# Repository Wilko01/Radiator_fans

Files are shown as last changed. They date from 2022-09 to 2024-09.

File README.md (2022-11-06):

# Radiator fan controlled
The radiator fan is used to control the airflow of the radiators to be able to heat the house via low temperatures.

Pictures of the parts

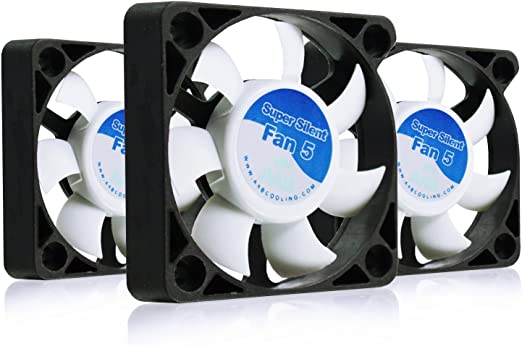
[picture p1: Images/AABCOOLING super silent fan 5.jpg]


## Description and operation instructions
The fans are turned on when a certain temperature of the radiator is detected and turned off when it is below another temperature value. The fans are controlled via different levels where at lower temperature levels the fan runs at a lower speed and when the temperature level is high the fan runs at a higher speed. The logic is running on the ESP32. To be able to override the logic there is an override variable which enables remote control and bypasing the ESP32 fan control. 
The fans are modular build where the first unit is the master which has 3 fans and the micro controller ESP32. It can be extended with a number of modules which act as slaves. Each module contains 3 fans. Tested with a maximum of 4 modules. 1 master and 3 slaves.

 ## Technical description
The ESP32 provides an analogue value which is fed into a transistor. The transistor amplifies the voltage and is typically operating between 5V and 12V. Lower than 5V will stop fans as they are not PWM fans. The ESP32 is running ESPHOME and connected to Home Assistant. The sensor for the temperature is included in the master module. Slaves will get the analogue value from the master and amplified it via the transistor. A trim potential meter is used to tune the master and slave modules as there are voltage losses when connecting multiple modules. By tuning the speed of all fans of all modules can be aligned. Best is to set the 500 Ohm potential meter to 250 Ohm before soldering it in. This provides space to tweak. See the next paragraph for the calibration of the fans.
The master with its slaves run independent of Home Assistant, but could be overwritten by an override variable.
The ESP32-wroom-32U was chosen as it has an external antenne which can be brought to the front of the radiator to receive a better wifi signal.
Calculation of the resistor to connect the BD139 to the ESP32
	ESP 32 delivers max 40mA per pin at 3,3V
	The DB139 has the following specs:
		Emitter - base 0,5A at a voltage of max 5V
	3,3V max / 20mA = 165 Ohm.
	Selected 150 Ohm as I have that in stock
Measuring the RPM via the ESP32 is okay till the voltage drops below 10V as the RPM signal then becomes too weak. When the RPM is measured then it also consumes power and the fan will earlier stop to spin then the other fans which are connected when the voltage is lowered.
The fan that I use is a more expensive one. It is quite, has a high airflow with low current and a high 100.000 hours estimated runtime. Comparing it to a € 1,5 fan, the cheap fan is way less quite, do have a higher airflow, which I doubt if it is needed and uses twice the amount of current. With the calculation that I made the more expensive fan will become equal after 2 years while the fan then for the remainder of its lifetime consumes less power.
Use a 1k resistor behind RPM. If not then the other fans keep spinning when off.
Power lines red and black are 24AWG, Rest is 28AWG. Cables to connect the modules are 24AWG as that is easier to connect the (Dupont) JST pins to.

The code can be found at the end of this page. Specifics like the modification of the temperature sensor address are described at the code block.

### Calibration of the fans
When all modules are connected to the master, spin the fans and connect a scope with multiple channels if you have one with the positive of the scope to the 12V and the negative to the negative side of the capacitor which is parallel to the fans. Tune the voltages via the potential meters so they are almost the same in the upper and lower speeds of the fans. If you don't have a scope, then use preferrably multiple multimeters to measure the voltages and tune. It is also possible to use one multimeter, but you need to measure, tune and measure the other modules one by one.

Calibrate fans at min speed. Blue spikes in the background idicate that the scope signals are laying on top of eachother.

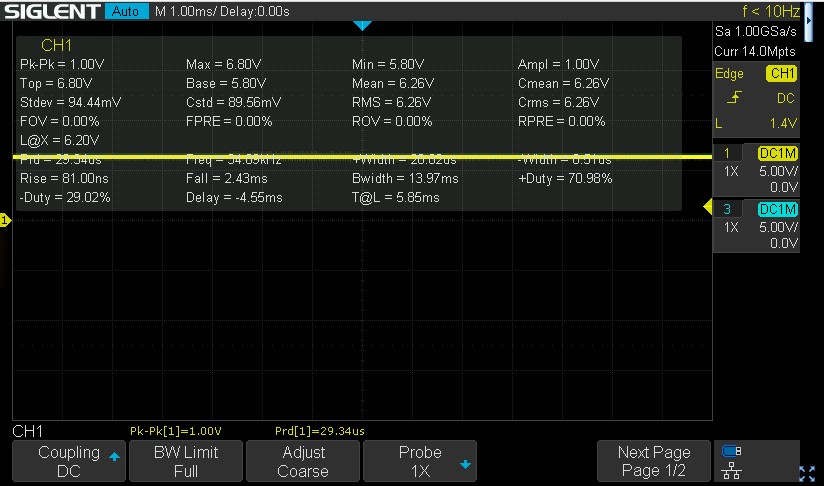
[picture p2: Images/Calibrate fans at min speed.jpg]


Calibrate fans at max speed. Blue spikes in the background idicate that the scope signals are laying on top of eachother.

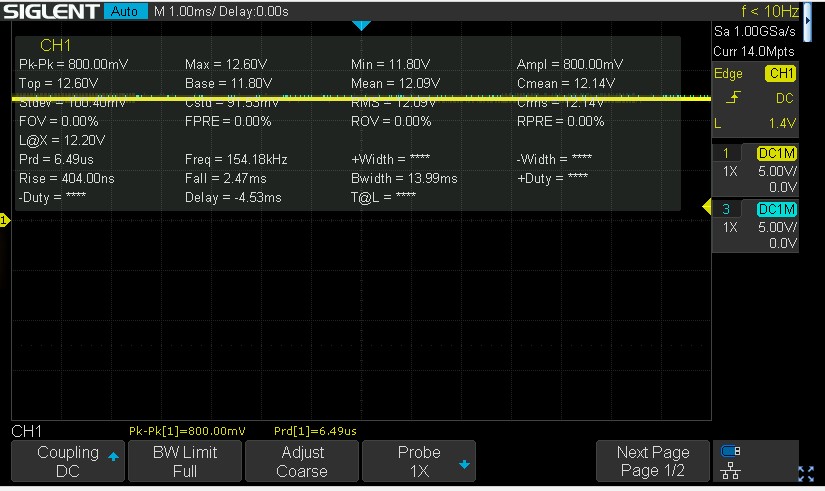
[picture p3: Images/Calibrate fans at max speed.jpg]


Calibrate fans where the signals are slightly misaligned.

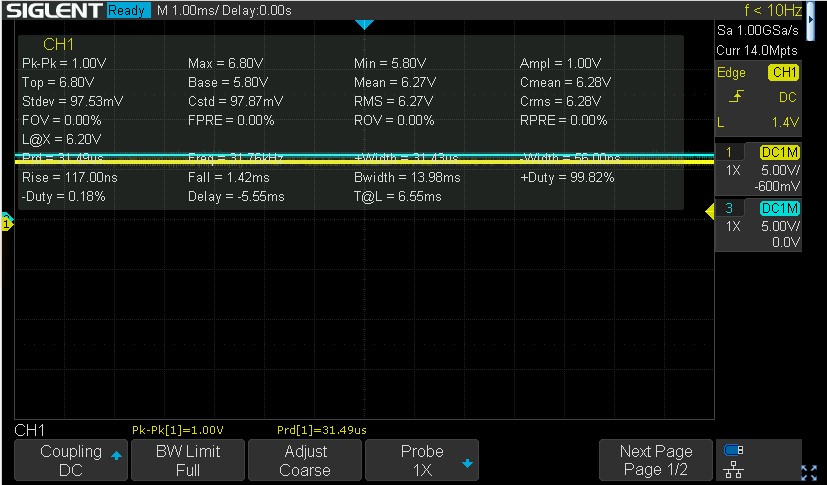
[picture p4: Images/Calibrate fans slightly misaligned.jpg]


### Parts

Multiple colored silicon cables AWG 24 and 28

#### Master module
3 x Fan AABCOOLING Super Silent Fan 5



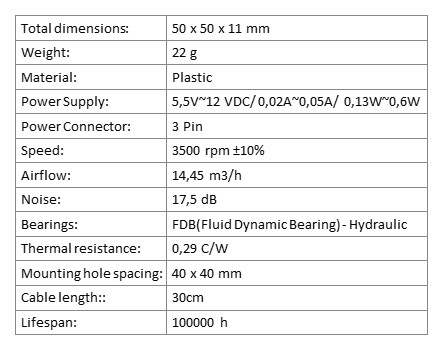
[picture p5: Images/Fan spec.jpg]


Fan pinout pinout
- 12V = Red
- GND = Black
- RPM = Yellow

1 x ESP32

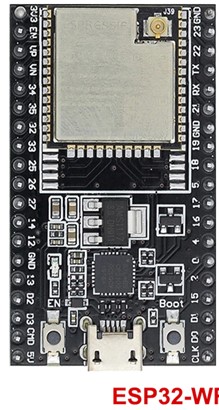
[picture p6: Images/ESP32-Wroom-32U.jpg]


Dallas DS18B20 temperature sensor

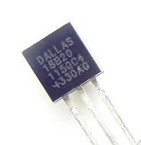
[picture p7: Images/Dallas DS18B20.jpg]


1 x BD139 NPN transistor

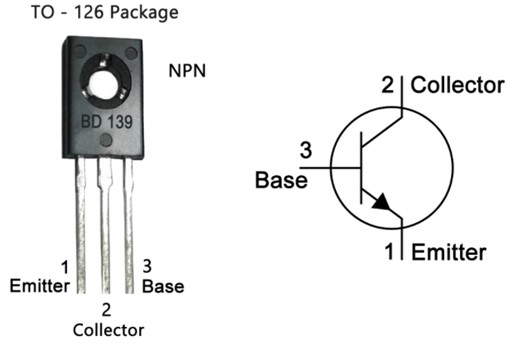
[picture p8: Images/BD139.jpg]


1 x BC549 NPN transistor (option for leds)

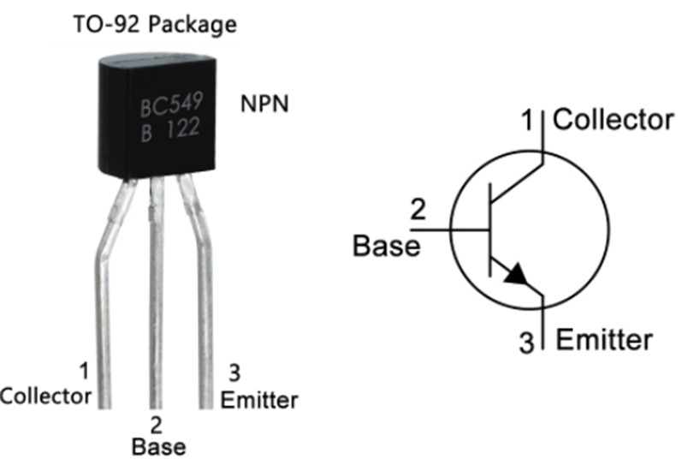
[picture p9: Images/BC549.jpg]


Heatsink TO220

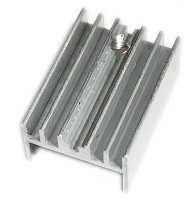
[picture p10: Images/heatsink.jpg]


1 x Mini360 DC- DC buck converter

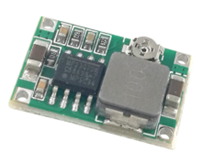
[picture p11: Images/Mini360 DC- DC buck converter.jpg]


PCB 4 x 6 Used to mount the ESP32

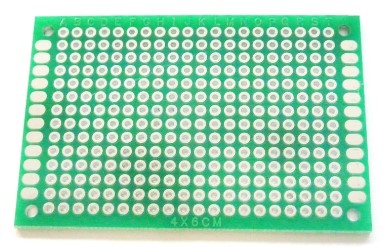
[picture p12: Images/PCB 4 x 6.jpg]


PCB 2 x 8 Used to connect the JST to and to mount the transistor(s)

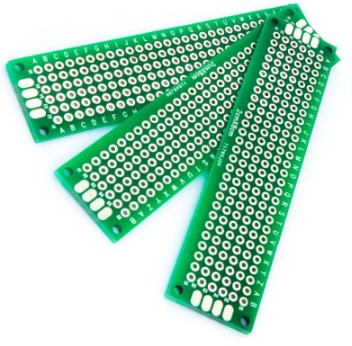
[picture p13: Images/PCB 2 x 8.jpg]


Trim potentiometer R 500 



Resistors
- 1 x 47hm (option for leds)
- 1 x 150
- 2 x 1k
- 1 x 1k (option for leds)
- 1 x 4k7

- 1 x 1000u capacitor

2 x 5mm Warm White led (option)

Magnets
- 12 x 6 mm

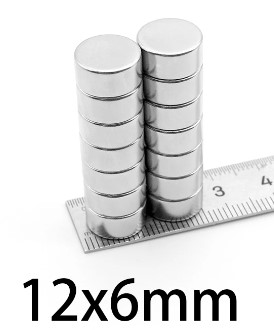
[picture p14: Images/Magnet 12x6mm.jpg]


- 8 x 4 mm

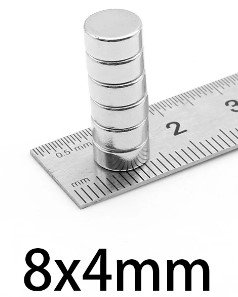
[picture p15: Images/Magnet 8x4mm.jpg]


- 1 x screw M2x8mm

- 4 x screw M2x6mm

- 1 x 12V DC adapter

- 1 x 5 pin JST male - female connector

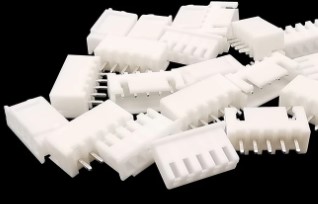
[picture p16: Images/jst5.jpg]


1 x 5.5 x 2.1 Female DC power plug

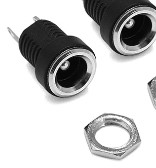
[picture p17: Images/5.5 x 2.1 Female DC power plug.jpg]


#### Slave module
3 x Fan AABCOOLING Super Silent Fan 5



1 x BD139 NPN transistor



1 x BC549 NPN transistor (option for leds)



Heatsink TO220



PCB 2 x 8 Used to connect the JST to and to mount the transistor(s)



Trim potentiometer R 500 Ohm W501



- 1 x 47hm Resistor (option for leds)

- 1 x 1000u capacitor

- 2 x 5mm Warm White led (option)

- 2 x 5 pin JST male - female connector



Magnets
- 12 x 6 mm



- 1 x screw M2x8mm

- 2 x screw M2x6mm

### Schematic overview
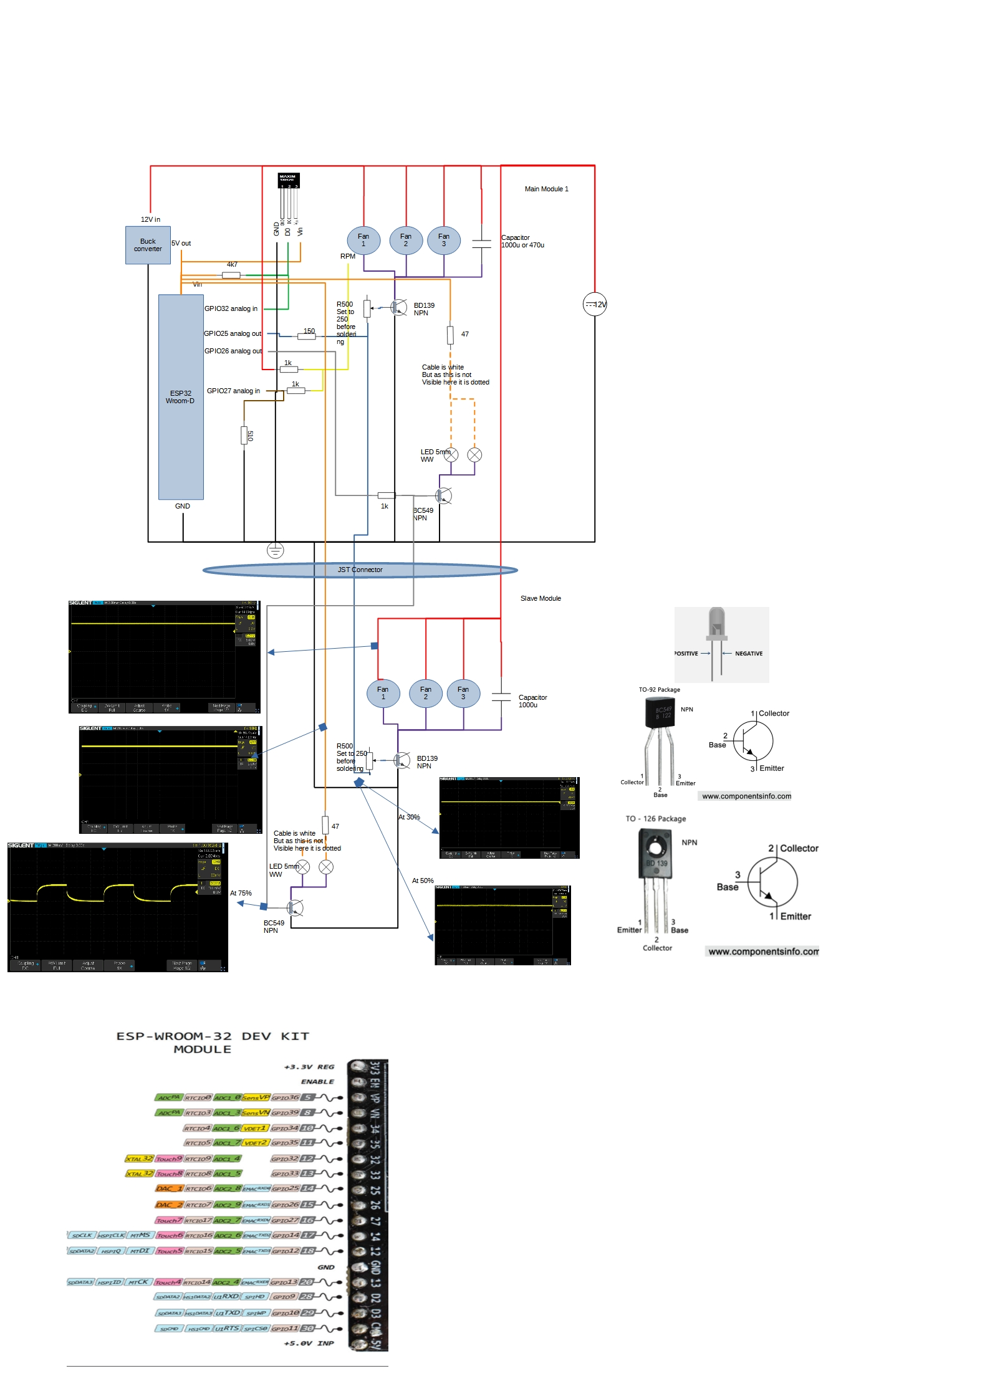
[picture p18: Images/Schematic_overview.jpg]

 
•	Power the circuit only via 12V and run code updates via OTA and ESPHOME.

### ESPHOME Configuration
### ESPHome Configuration in Home Assistant
Create a new ESPHOME device with this code:
### Code
[Code in ESPHOME](code radiator-huiskamer-voor.vbs)
Boot the ESP with the Dalles temperature sensor connected. This will show in the log at boot time the address of the connected Dallas sensor. Copy it and update the code with the retrieved address.

### 3D printer files
[3D Printer files](3D_Printer_Files)
As I have multipe radiators where some have different sizes I used the naming convention of the 3D files of the room(s). I made the files in Sketchup make and added this file as well.

### Code per radiator
The code of each radiator is the same except the name of the radiator. So just pick any of these files and adjust the name to reflect your situation.

[Code in ESPHOME for Huiskamer voor](code_radiator_huiskamer_voor.vbs)

[Code in ESPHOME for kleine kamer](code_radiator_kleine_kamer.vbs)

[Code in ESPHOME slaapkamer voor](code_radiator_slaapkamer_voor.vbs)

[Code in ESPHOME for gang](code_radiator_gang.vbs)

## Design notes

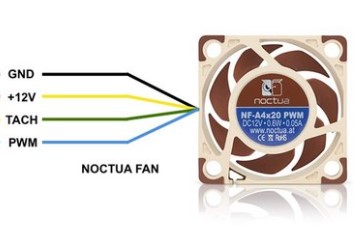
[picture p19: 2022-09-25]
Images/Noctua fan PWM pinout.jpg

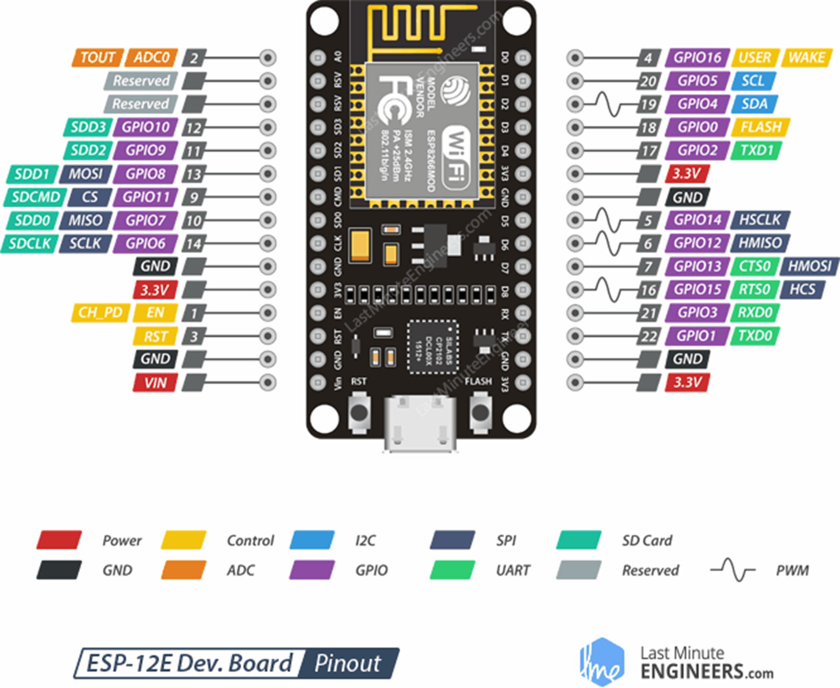
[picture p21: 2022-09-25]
Images/ESP8266_NodeMCU.jpg

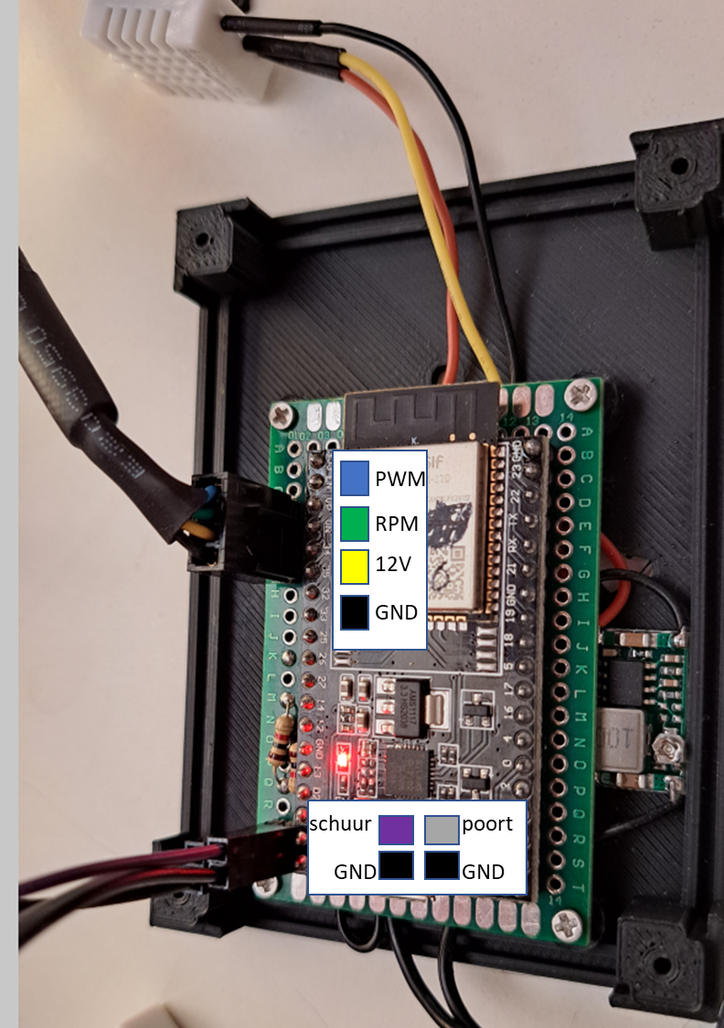
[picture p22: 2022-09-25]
Images/ESP32_connectors.jpg

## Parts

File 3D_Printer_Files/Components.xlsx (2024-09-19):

 |  | Implemented
 |  | Green is ready to be mounted
 |  | Oranje is printed |  |  |  |  |  |  |  | Amount of fans needed for the room: |  |  | https://www.speedcomfort.nl/ | https://heatfan.eu/ Has a configurator on their website, but they mention tons of units needed to heatup (https://heatfan.eu/%20Has%20a%20configurator%20on%20their%20website,%20but%20they%20mention%20tons%20of%20units%20needed%20to%20heatup)
 |  |  | Hoogte cm | Breedte cm | Master | Extension | Slave | Extension | To be printed | According to Speedcomfort the air in the room needs to be refreshed once per hour. Their unit moves 30m3/h. So for a room of 8x4x3 = 96 m3. A minimum of 3 speedcomfort units is needed. The unit that I made transfers per fan max 14,5m3. It is not desired that it runs at 100%, but on the other hand the lowest value is 55 a 60% due to the startup voltage needed. The master with extension has 3 fans, assume it runs at 60% with a airflow of 3x14.5x0.5=21.75 as minimum and 3x14.5=43.5 maximum with noise of the fans.
 |  | Huiskamer voor | 40 | 265 | 1 | 1 | 3 | 3 |  | Woonkamer = ~ 8x4x2.7=86.4 m3. Meaning that for half power a minimum of 4 units is needed (12fans).
 |  | Huiskamer achter | 200,5 | 44,5 | 0 | 0 | 0 | 0
6 |  | Gang | 99 | 84 | 1 | 1 | 1 | 0 Special one
6 |  | Kleine kamer | 60 | 80 | 1 | 1 | 1 | 0 Special one | al getekend en past mogelijk ook op de gang
 |  | Master Bedroom | 60 | 168 | 0 | 0 | 0 | 0
9 |  | Tessa. vervallen is naar douche gegaan | 60 | 168 | 1 | 1 | 2 | 2 |  | Tessa = ~ 3.5x4x2.2=30.8 m3. Meaning half power 2 units are needed
 |  | Douche | 60 | 84 | 1 | 1 | 0 | 0
 |  | Zolder | 100 | 144 | 0 | 0 | 0 | 0
 |  |  |  | Total | 5 | 5 | 7 | 5
 |  |  |  |  |  |  |  |  |  |  | Green means already ordered or available
Component list |  |  |  |  |  |  |  |  |  |  |  |  |  |  | 181
Total | Master module with extension |  |  |  |  |  |  |  |  |  | Total remaining order |  |  | Unit costs | Rough costs
15 | 3 | fans |  |  |  |  |  |  |  |  | 21 | fans |  | 5 | 105
15 | 3 | magnets 12*6 round |  |  |  |  |  |  |  |  | 33 | magnets 12*6 round |  | 22 | 22
5 | 1 | magnet 8*4 for the dallas sensor |  |  |  |  |  |  |  |  | 11 | magnet 8*4 for the dallas sensor |  | 10 | 10
5 | 1 | magnet 8*4 for the wifi antenna |  |  |  |  |  |  |  |  | 4 | magnet 8*4 for the wifi antenna |  | 0 | 0
5 | 1 | 12V voeding |  |  |  |  |  |  |  |  | 4 | 12V voeding |  | 0 | 0
5 | 1 | 12V connector |  |  |  |  |  |  |  |  | 4 | 12V connector |  | 1 | 1
5 | 1 | JST connector 5 pins |  |  |  |  |  |  |  |  | 18 | JST connector 5 pins |  | 4 | 4
5 | 1 | Printplaat 40*60 |  |  |  |  |  |  |  |  | 4 | Printplaat 40*60 |  |  | 3
5 | 1 | esp32 met antenne |  |  |  |  |  |  |  |  | 4 | esp32 met antenne |  |  | 25
5 | 1 | BD139 |  |  |  |  |  |  |  |  | 11 | BD139 |  |  | 4
5 | 1 | 1000uF |  |  |  |  |  |  |  |  | 11 | 1000uF |  |  | 2
5 | 1 | dallas 18B20 |  |  |  |  |  |  |  |  | 11 | dallas 18B20 |  |  | 5
5 | 1 | buck converter of LM317 |  |  |  |  |  |  |  |  | 4 | buck converter |  |  | 0
5 | 1 | screw flat head M2x8 to connect the extension |  |  |  |  |  |  |  |  | 11 | screw flat head M2x8 to connect the extension
20 | 4 | screw flat head M2x6 to mount the PCB |  |  |  |  |  |  |  |  | 44 | screw flat head M2x6 to mount the PCB
15 | 3 | 5mm RGB led |  |  |  |  |  |  |  |  | 33 | 5mm RGB led
 |  |  |  |  |  |  |  |  |  |  | 11 | BD139
 |  |  |  |  |  |  |  |  |  |  |  | heatsink
 | Slave module with extension |  |  |  |  |  |  |  |  |  |  | Cabling
21 | 3 | fans |  |  |  |  |  |  |  |  | 7 | Printplaat 20*80
21 | 3 | magnets 12*6 round
7 | 1 | magnet 8*4 for the dallas sensor
14 | 2 | JST connector 5 pins om deze en volgende module aan te sluiten
7 | 1 | Printplaat Voor de BD139, condensator, weerstand, etc
7 | 1 | BD139
7 | 1 | 1000uF
7 | 1 | dallas 18B20
7 | 1 | screw flat head M2x8 om de extension te koppelen
14 | 2 | screw flat head M2x6 to mount the PCB
21 | 3 | 5mm RGB led

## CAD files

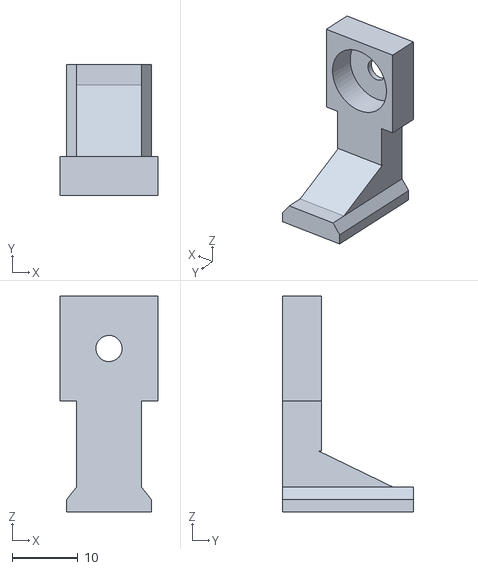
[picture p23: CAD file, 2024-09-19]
3D_Printer_Files/Connection with magnet extra high for douche.stl
15.0 x 20.0 x 32.9

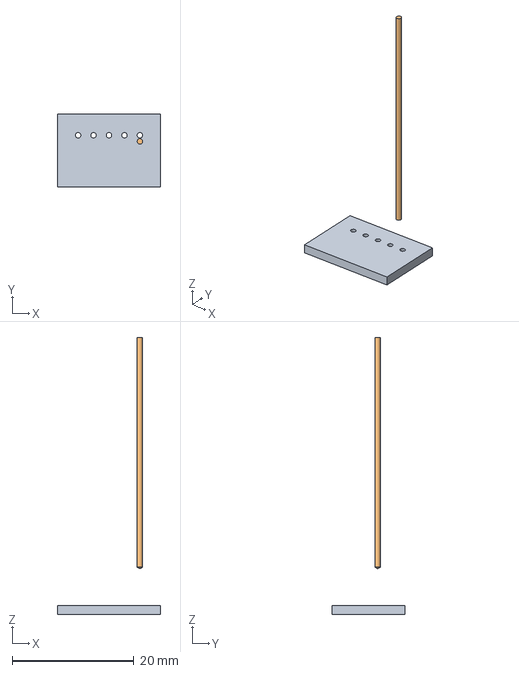
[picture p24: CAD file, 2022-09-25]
PCB connector drilling gaps.FCStd
17.0 x 12.0 x 45.5 mm
CutTool

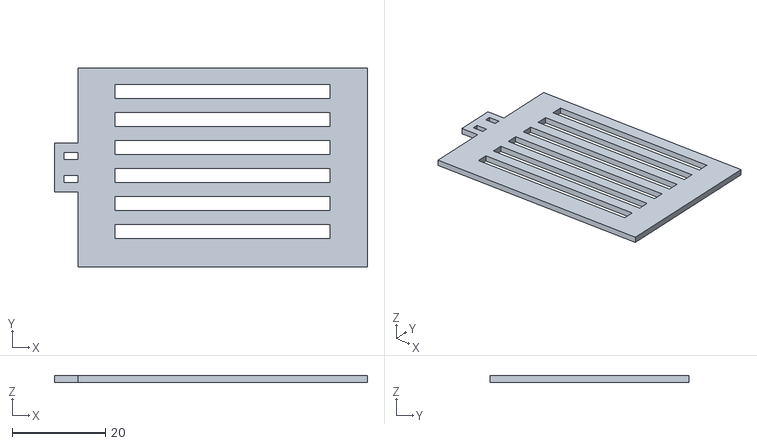
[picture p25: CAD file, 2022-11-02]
3D_Printer_Files/Kleine kamer en gang master module cover at the bottom.stl
67.0 x 42.5 x 1.50

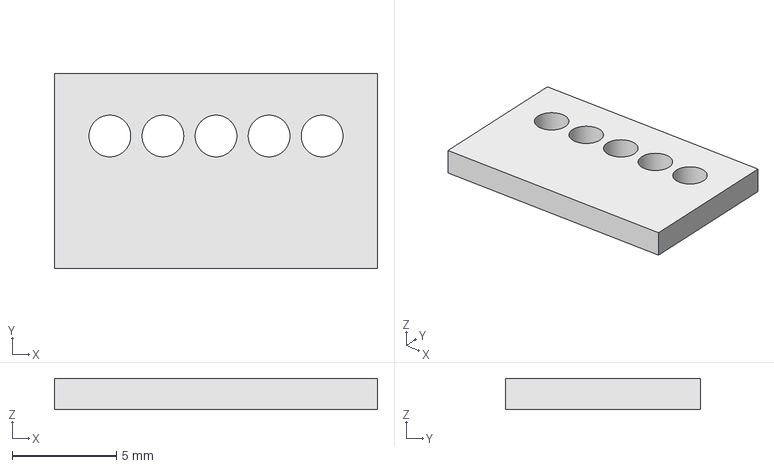
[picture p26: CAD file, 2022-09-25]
PCB connector without drilling gaps.FCStd
15.5 x 9.35 x 1.50 mm

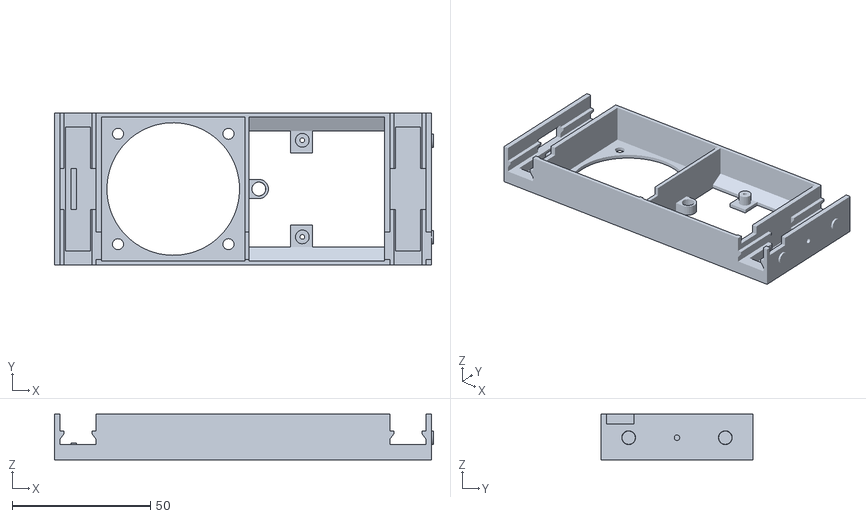
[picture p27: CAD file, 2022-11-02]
3D_Printer_Files/Gang slave module.stl
137.2 x 55.0 x 16.5

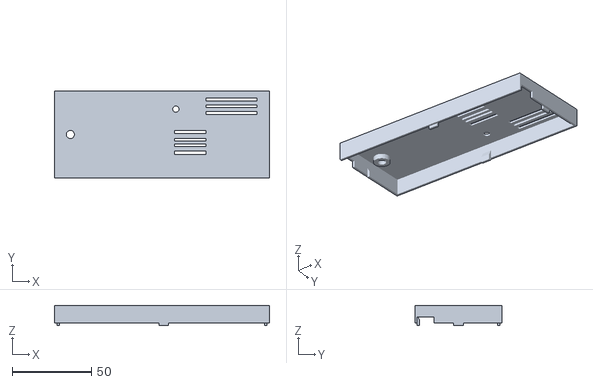
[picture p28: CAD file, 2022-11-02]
3D_Printer_Files/Huiskamer en Tessa master module cover at the top.stl
135.5 x 55.0 x 12.7

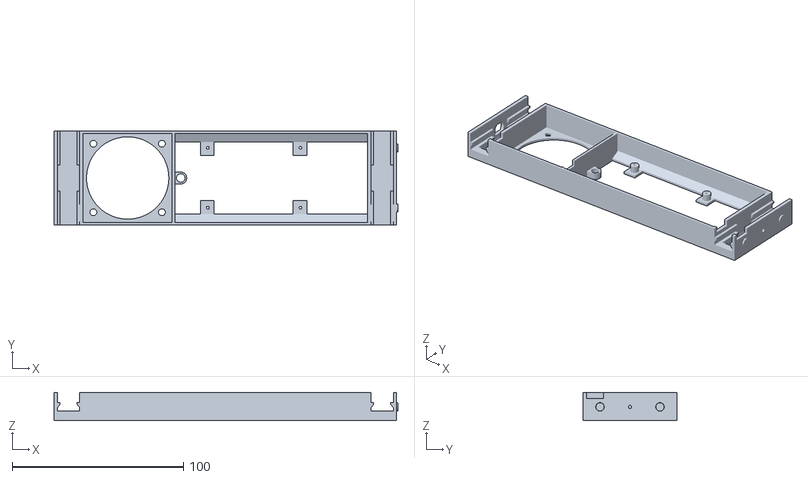
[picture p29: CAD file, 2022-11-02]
3D_Printer_Files/Kleine kamer en gang master module.stl
200.7 x 55.0 x 16.5

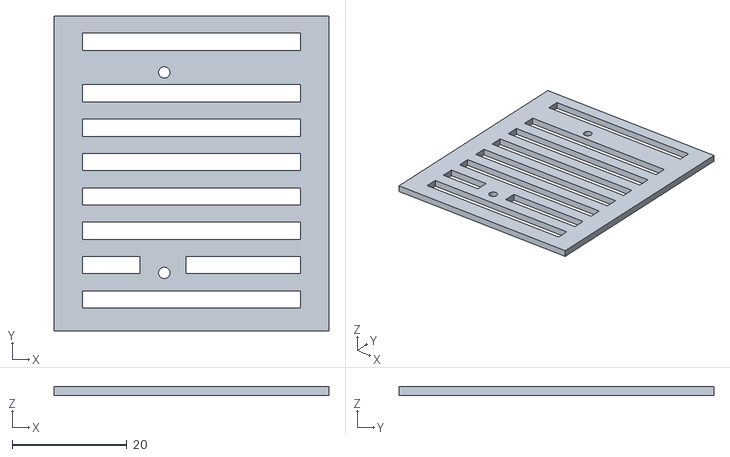
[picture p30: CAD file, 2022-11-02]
3D_Printer_Files/Gang slave module cover at the bottom.stl
48.0 x 55.0 x 1.50

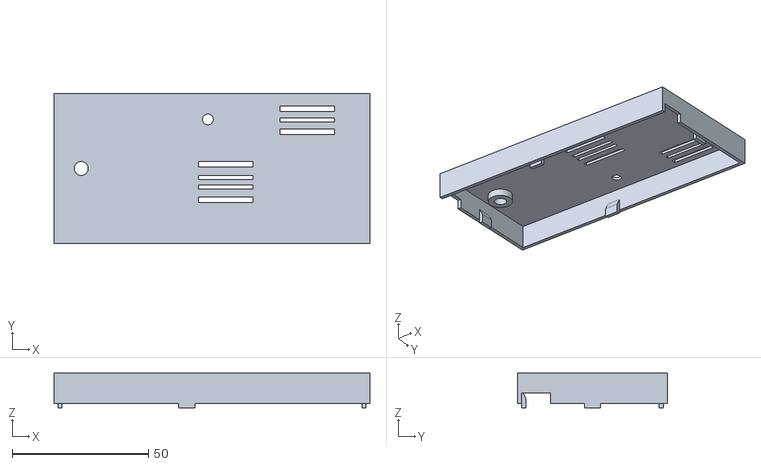
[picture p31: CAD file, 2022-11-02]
3D_Printer_Files/Kleine kamer en gang master module cover at the top.stl
116.0 x 55.0 x 12.7

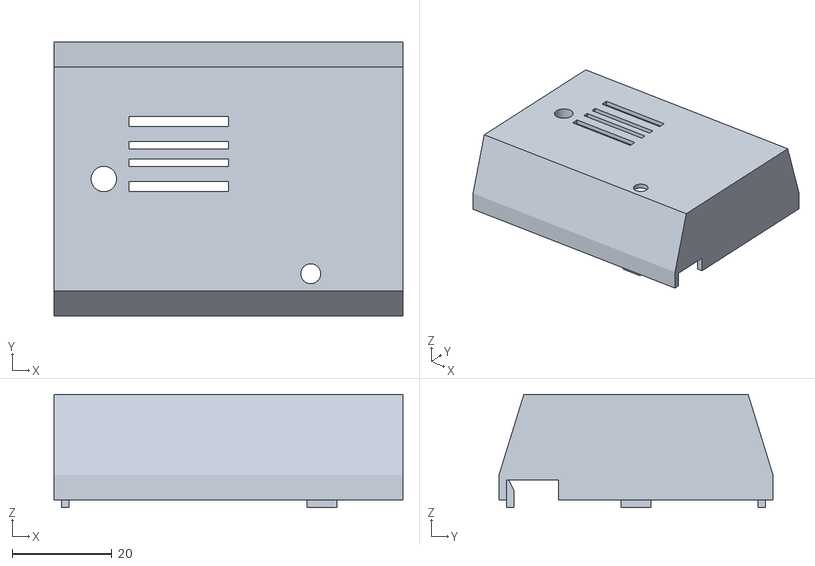
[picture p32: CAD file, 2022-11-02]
3D_Printer_Files/Huiskamer en Tessa slave module cover at top.stl
70.0 x 55.0 x 22.7

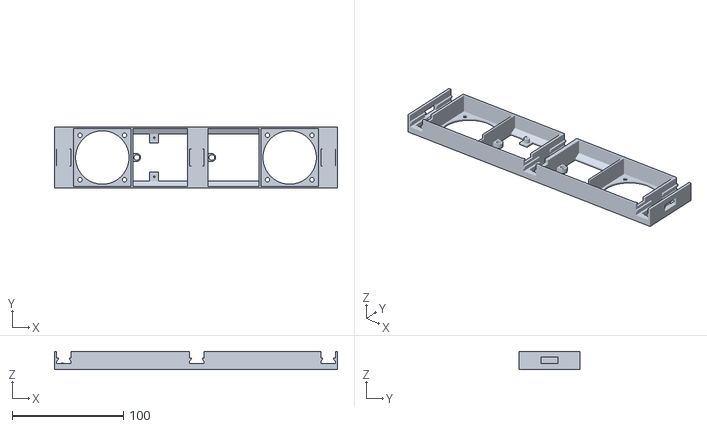
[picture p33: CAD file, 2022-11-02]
3D_Printer_Files/Kleine kamer slave with extension module.stl
254.5 x 55.0 x 16.5

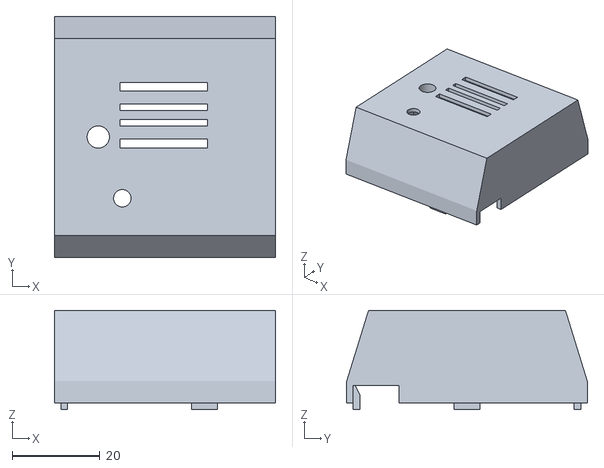
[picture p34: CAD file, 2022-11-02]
3D_Printer_Files/Kleine kamer slave with extension module cover at the top.stl
50.5 x 55.0 x 22.7

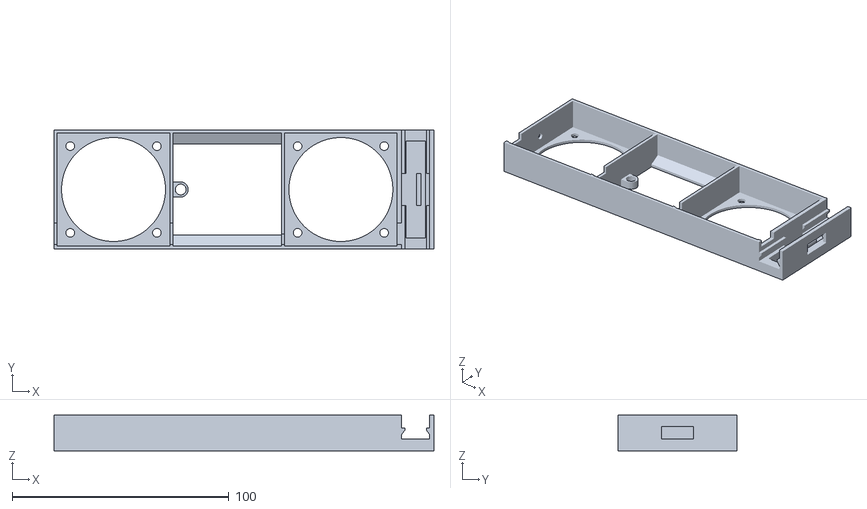
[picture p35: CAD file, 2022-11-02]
3D_Printer_Files/Kleine kamer en gang master module extension.stl
175.5 x 55.0 x 16.5

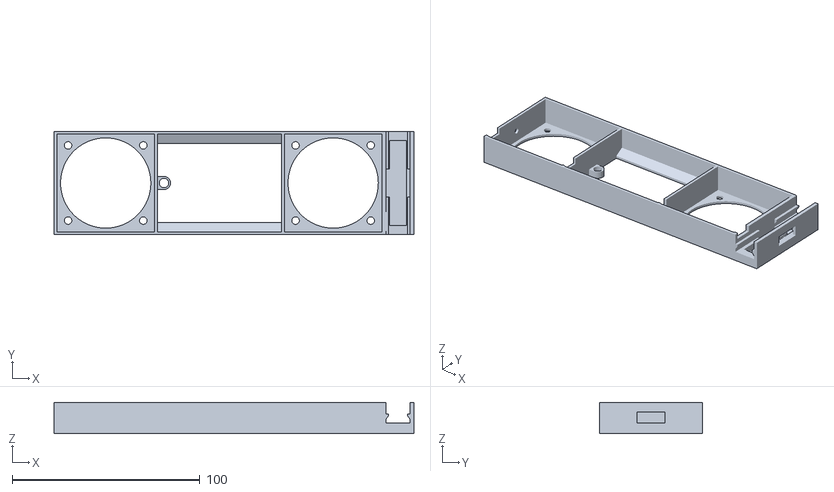
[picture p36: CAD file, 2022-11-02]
3D_Printer_Files/Gang slave module extension.stl
191.5 x 55.0 x 16.5

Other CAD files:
3D_Printer_Files/Kleine kamer slave with extension module cover at the bottom.stl
3D_Printer_Files/Huiskamer en Tessa master module cover at the bottom.stl
3D_Printer_Files/Huiskamer en Tessa slave module cover at bottom.stl
3D_Printer_Files/Gang slave module cover at the top.stl
3D_Printer_Files/Bus 2mm hoog.stl
3D_Printer_Files/Bus 3mm hoog.stl
3D_Printer_Files/Bus 4mm hoog.stl
3D_Printer_Files/Connection with magnet.stl
3D_Printer_Files/Huiskamer en Tessa master module.stl
3D_Printer_Files/Huiskamer en Tessa master or slave extension module.stl
3D_Printer_Files/Old/Radiator fan 03.skp
3D_Printer_Files/Old/Radiator fan 04.skp
3D_Printer_Files/Old/Radiator fan 05.skp
3D_Printer_Files/Old/Radiator fan 06.skp
3D_Printer_Files/Radiator fan 03.skp
3D_Printer_Files/Radiator fan 04.skp
3D_Printer_Files/Radiator fan 06.skp
3D_Printer_Files/Radiator fan 07.skp
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

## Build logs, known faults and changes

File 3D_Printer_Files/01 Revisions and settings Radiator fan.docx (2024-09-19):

# Print settings:

- Print material: PLA
- Rotation of the objects: rotate the ‘Radiator fan magnet’ 90 degrees so it doesn’t need support
- Support: Yes
- Skirt, brim: Skirt.
- Infill: 20%

# Additional instructions

- None

# Materials needed

- PLA, preferred ABS, but as that is more difficult to print I used PLA and will experience if this will last.

# Log history

# Version 0.7

- Made additional magnet connection which is extra high for the douche. ‘Connection with magnet extra high for douche’

# Version 0.3

- Made a stop for the JST 5 pins connector
- Created a raster for underneath the ESP
- Adjusted the height of the LED fitting by 1mm
- Adjusted the screw hole for the mounting of the PCB from 0.75 to 0.85 radius

# Version 0.2

- Made the gaps at each head size slightly bigger as the connectors did not fit in properly
- Made the mounting holes of the screws for the ESP in the bottom plate wider to better fit the screw and enlarged the width of the body where the screw is inserted. Adjusted the height and position of the ESP32 so the ESP is looking downwards
- Added a blocker to stop the JST connector at the head of pushing in
- Made the extension use the same connection bars in the middle for strength and possible PCB connection
- At the master removed the middle part of the extension as it will be strong by the PCB on top of it and without the middle part there is room to access the ESP

# Version 0.1

- First release

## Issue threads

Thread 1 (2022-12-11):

Radiator Wide

TheNavy, 2022-12-11:
Hello,
I am looking for just such a project. Unfortunately, without printing it, I can't tell how wide the radiator needs to be inside to fit your modules. My German radiators are ~70mm wide inside.

TheNavy, 2022-12-13:
I have made a test print. It fits ;)

Wilko01, 2022-12-13:
Hi,
Sorry for the late response. It is a bit wider than 50mm as the used fans are 50mm and the sides are about 1,x mm. Having 70mm space should always fit. Please let me know if you need the exact details as they are in the drawings, but I don't have my laptop at hand to check.

Wilko01, 2022-12-13:
provided the necessary information

Closed 2022-12-13.

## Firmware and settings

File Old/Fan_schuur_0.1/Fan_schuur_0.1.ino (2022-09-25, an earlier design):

int potPin = 0; // Analog in 0 connected to the potentiometer
int transistorPin = 9; // PWM Pin 9 connected to the base of the transistor
int potValue = 0; // value returned from the potentiometer
 
void setup() {
  // set the transistor pin as output:
  pinMode(transistorPin, OUTPUT);
}
void loop() {
  // read the potentiometer, convert it to 0 - 255:
  potValue = analogRead(potPin) / 4;
  // use that to control the transistor:
  analogWrite(transistorPin, potValue);
}

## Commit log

2022-10-02 Added 3D print files
    [Bus 2mm hoog.stl, Bus 3mm hoog.stl, Bus 4mm hoog.stl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]
2022-10-29 Updated tacho connection
    [Components.xlsx, Gang Radiator fan salve module 03.stl, Gang Radiator fan slave extension module 03.stl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]
2024-09-19 Updated the describtion of the resistor before the BD139
    [Components.xlsx, Connection with magnet extra high for douche.stl, Radiator fan 06.skp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]
